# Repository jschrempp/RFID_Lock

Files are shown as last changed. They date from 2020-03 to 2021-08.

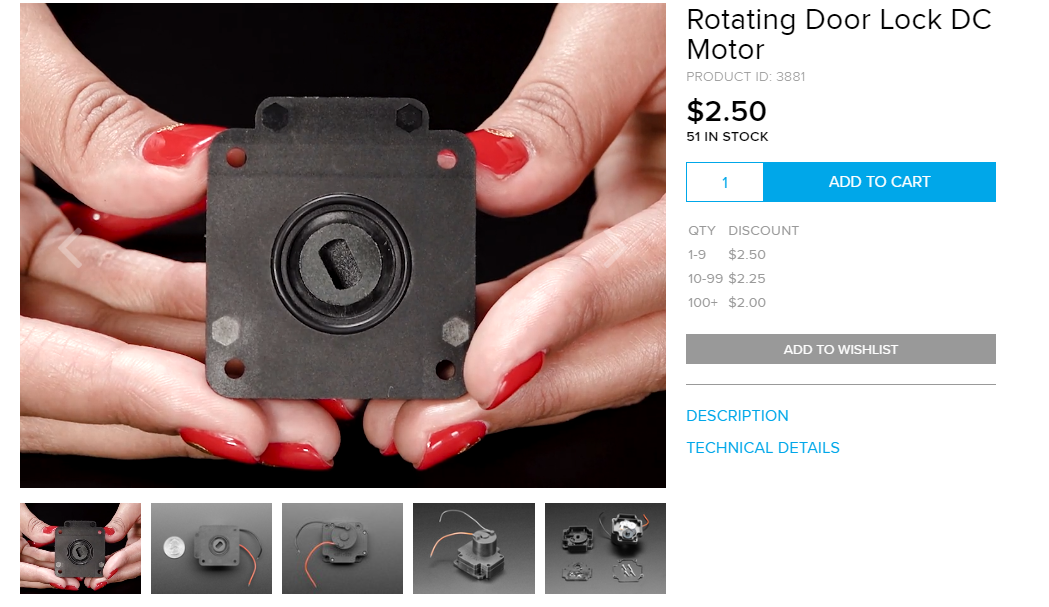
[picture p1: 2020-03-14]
Hardware/Other_Mechanisms/Adafruit_lock.png

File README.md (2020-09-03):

# RFID_Lock

Hardware and firmware for a Photon-based device that can control various locking mechanisms.

The device subscribes to publications with the name "checkin". These events are published by an RFID Station. 
The event data is JSON encoded and includes the deviceType of the publisher, as well as a secret security key.

Each lock station is configured via an App (or via the Particle Cloud) to act on a checkin event from a particular deviceType. 
If the event contains the correct deviceType and the correct secret key, then this device will unlock a cabinet, door, machine or power.

## Story
Our MN_ACL project (https://github.com/TeamPracticalProjects/MN_ACL) creates an infrastructure for secure, 
RFID-based access control to a Makerspace and it's various internal equipment locations.  That project integrates
Particle Argon-based RFID stations with a commercial cloud CRM system and an internal tracking database.
The MN_ACL project ensures that people who access the facility are paid up members in good standing and that
members who access certain locations containing sophisticated industrial equipment have basic operating 
and safety instruction credentials.  The project controls access via red/green lit buttons and an audible beeper.

Certain locations within the Makerspace contain expensive materials, parts and accessories.  We decided to create 
a Particle Photon-based add-on that could subscribe to publications sent by the Argons in the RFID stations
and unlock cabinets containing these expensive accessories.  We therefore needed to find an inexpensive but 
effective electrically controlled locking mechanism and create a Photon-based printed circuit board (and
associated Particle firmware) to unlock the cabinet when a member taps into one of the relevant RFID
stations with credentials that allow them access to these accessories.

COVID-19 related health and safety regulations require that the front door be locked to the outside and 
access to the facility be controlled. There is a 24 volt (DC) solenoid in the door mechanism that is wired 
back into the facility equipment room.  We determined that mounting an RFID station at the front entrance and 
using the same publish/subscribe mechanism as for cabinet locks, we could remotely and securely activate the front 
door solenoid lock to admit members when they tap their badge to the front door RFID station.

We decided to generalize this mechanism as much as possible in order to accommodate other access control requirements as
they arise in the future.

We decided that we needed a separate WiFi enabled circuit board for this purpose because:

1. The relationship between RFID stations and cabinets/locks is many to many.

2. Hardwiring a lock control signal from an RFID station to certain cabinets or locks is both inconvenient
and easily hacked.

3. A general-purpose, secure, WiFi enabled locking mechanism is a worthwhile and useful project
in and of itself, independent of the MN_ACL project and it's RFID stations.

We selected the Particle Photon for this project because it provides a low cost and secure means of WiFi
control and communication and because of Particle's simple and elegant cloud communication capabilities.

## Locking Mechanisms
### Locking a cabinet
We investigated a number of solutions for electrically controlled locking mechanisms and we ultimately
decided to hack an off-the-shelf mechanism from Tokatuker; see: 
https://www.amazon.com/Tokatuker-Electronic-Cabinet-Hidden-Drawer/dp/B075QF1VPR

The Tokatuker cabinet lock is a complete RFID solution in itself, but it does not have the required 
security or database integrations required for this project.  We therefore removed the electronics 
and provided our own Photon-based hardware to control the lock.  We also removed the batteries and 
we power the Tokatuker mechanism from our hardware so that the cabinets would not be stuck locked 
if a battery runs down.

We chose the Tokatuker solution because the locking mechanism itself is very innovative and uses only
a small, low power DC motor to control a mechanically robust locking system.  We found that pulsing this
motor for 30 milliseconds in one direction unlocks the lock and pulsing it for 30 milliseconds in the 
opposite direction re-locks the lock.  Unlocking the lock springs the cabinet door open and the door can
thereafter be closed and will lock anytime after the small motor returns to the locked position. The 
device can therefore unlock, opening the cabinet door, and then immediately re-lock and the door can 
be closed and will automatically lock at any time thereafter.

### The front door
The facility front door has a locking pushbar that includes a solenoid for remote unlocking.  This solenoid
was already wired back to the facility's equipment room. We experimentally determined that activating the 
solenoid for 2 seconds after a successful RFID card tap-in by a member in good standing is more than sufficient 
to provide entry to the facility.

### Our documentation
This project contains complete instructions for building an RFID Lock using the Tokatuker product.  This
project also contains instructions and firmware for activating a door-unlocking solenoid.
We also investigated various other locking mechanisms based upon servos, solenoids, etc.
We have included some information about these other approaches in this repository but we cannot
supply complete mechanics and Particle firmware to use them, as we did not carry these other locking
solutions through to a complete project solution.

## Electronics
We developed a printed circuit board that houses a Photon and integrates the Photon with components
that allowed us to test out various locking solutions.  This printed circuit board seemed so generally
useful to us that we have made it a project unto itself.  See: 
https://github.com/TeamPracticalProjects/Wireless_IO_Board

This project uses the Wireless_IO_Board hardware and we have added the Particle firmware necessary
to subscribe to publications from MN_ACL RFID Stations.  The documentation included with this project
provides ample references to these other projects where necessary.  Two sets of firmware are documented:
(1) firmware to respond to valid check-in events and unlock the modified Tokatuker motor lock.
(2) firmware to respond to valid check-in event and activate a door unlock solenoid.

## Mechanics
The modifications to the Tokatuker lock are documented in this repository.  Likewise, instructions
are provided for mounting the hardware in a small test cabinet that is demonstrative but also
useful in its own right.

## Firmware
This project includes Particle firmware (source code) for the Photon that integrates the RFID Lock
into the complete MN_ACL access control solution.

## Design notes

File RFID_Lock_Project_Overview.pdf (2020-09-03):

P a g e | 1

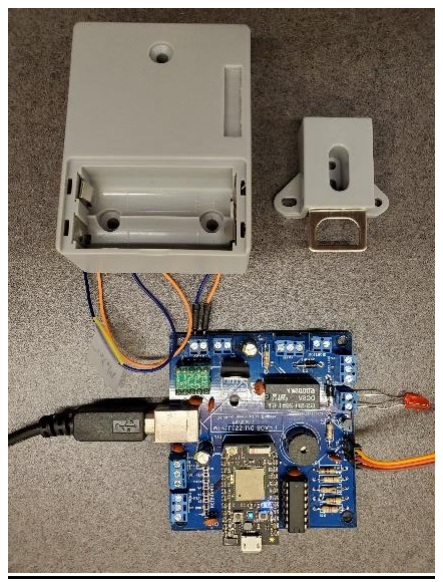
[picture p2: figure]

© 2020, Team Practical Projects, Jim Schrempp and Bob Glicksman; all rights reserved. Subject to “Terms of Use, License and Disclosure”

# RFID Lock Project Overview

By: Bob Glicksman, Jim Schrempp; v3, 8/30/20

© 2020 Team Practical Projects, Bob Glicksman and Jim Schrempp. All rights reserved.

NOTICE: Use of this document is subject to the terms of use described in the document “Terms_of_Use_License_and_Disclaimer” that is included in this release package. This document can be found at:

https://github.com/TeamPracticalProjects/Wireless_IO_Board/blob/master/Terms_of_Use_License_and_Disclaimer. pdf

© 2020, Team Practical Projects, Jim Schrempp and Bob Glicksman; all rights reserved.

## Contents

© 2020, Team Practical Projects, Jim Schrempp and Bob Glicksman; all rights reserved.

1.INTRODUCTION.

This document provides a brief overview of the RFID Lock project. Section 2 of this document describes the project in the context of the Maker Nexus RFID Access Control system project, and the Wireless I/O Board project, both of which are published at:

https://GitHub.com/TeamPracticalProjects

Section 3 of this document describes the layout of this repository and what information is included here.

2.RFID Lock Project Overview.

2.1. What this project is about.

This project is fundamentally about the hardware and firmware for a Particle¹ Photon-based device that can control various locking mechanisms. One specific locking mechanism has been fully implemented (see: https://www.amazon.com/Tokatuker-Electronic-Cabinet-Hidden-Drawer/dp/B075QF1VPR) (https://www.amazon.com/Tokatuker-Electronic-Cabinet-Hidden-Drawer/dp/B075QF1VPR) and is fully documented here. We have also implemented a solenoid lock activation mechanism to unlock a door. Other possible locking mechanisms have been briefly explored and some information about them has been included in the repository, albeit these other mechanisms have not been fully implemented and tested.

This project was specifically undertaken as an enhancement to the Maker Nexus RFID Access Control System (see: https://github.com/TeamPracticalProjects/MN_ACL). The concept is to have the MN_ACL RFID Stations publish a “check-in event” to the Particle cloud whenever a user taps into that Station with valid credentials. Every RFID Lock board subscribes to this event and compares the Station’s deviceType (included in the event) to its internally configured “Lock Listen code”. If the published deviceType matches the Lock Listen code, and if a secret key in the “check-in event” is valid, the device opens the lock. Depending upon the mechanical aspects of the lock in question, a cabinet or door may “pop open” when this happens, or else it may unlatch for some pre-specified period of time. A modified Tokatuker locking mechanism that has been fully implemented is of the type that pops a cabinet door or draw open. A solenoid controlled door unlocking mechanism has also been fully implemented and unlocks the door for a pre-specified period of time.

RFID Lock configuration can be performed via the MN_Station_Configurator App that is part of the MN_ACL project or via the Particle Console. Figure 1 below depicts the interactions of an

1 Particle.io

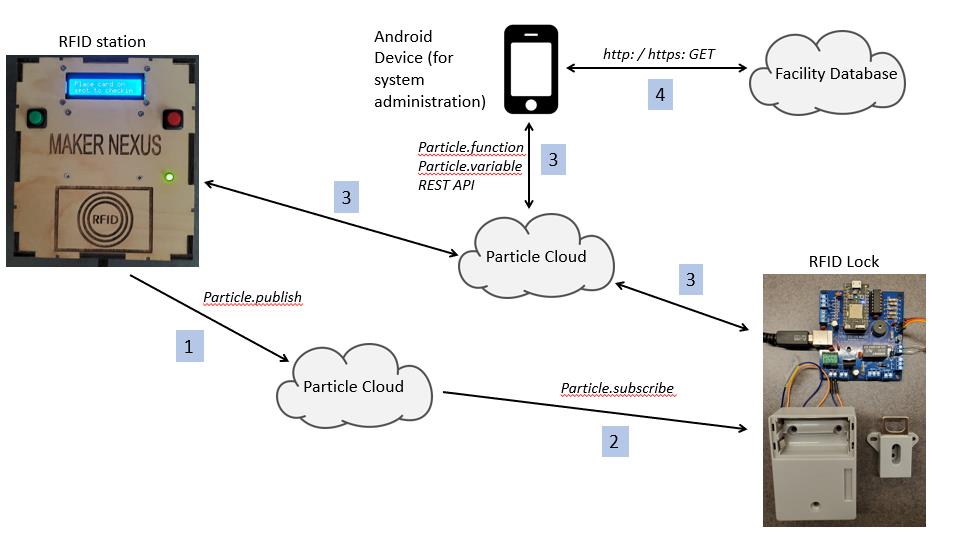
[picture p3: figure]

© 2020, Team Practical Projects, Jim Schrempp and Bob Glicksman; all rights reserved.

RFID Station, RFID Lock and MN_Station_Configurator App, all via the Particle Cloud. Further information about system operation can be found in the document:

https://github.com/TeamPracticalProjects/MN_ACL/blob/master/Documents/RFID_ACS_Overview_Document.pdf (https://github.com/TeamPracticalProjects/MN_ACL/blob/master/Documents/RFID_ACS_Overview_Document.pdf)

Figure 1. RFID Lock Architecture in Context of MN_ACS.

Referring to figure 1, the dataflows are:

(1). RFID Stations publish check-in events to the Particle cloud whenever a user taps in with a valid RFID card and the user is authorized to that Station’s function. The check-in event contains the RFID Station’s type and a facility secret key in a JSON encoded data set.

(2). RFID Locks subscribe to check-in events via the Particle cloud. When a check-in event’s deviceType data matches the Lock Listen code configured for the RFID Lock, and the check-in event’s secret key is valid, the RFID Lock unlocks the electromechanical lock to which it is wired.

(3). The MN_Station_Configurator App, running on an Android phone or tablet, allows a system administrator to configure deviceTypes into the RFID Stations, and both deviceTypes and Lock Listen Codes into RFID_Locks. The App does this by calling Particle cloud functions on these devices and the App obtains station configuration information by reading Particle cloud variables from these devices. The App (source code and install file) can be found at:

https://github.com/TeamPracticalProjects/MN_ACL/tree/master/Software/Android_Apps

© 2020, Team Practical Projects, Jim Schrempp and Bob Glicksman; all rights reserved.

The RFID Lock is made from a Photon based electronic printed circuit board and associated electromechanical locking hardware. The details of the printed circuit board are available in the following repository:

https://github.com/TeamPracticalProjects/Wireless_IO_Board

Although this project was driven by specific requirements of the Maker Nexus RFID Access Control project, the hardware, software and firmware may be useful in other contexts.

2.2. Story.

The MN_ACL project (https://github.com/TeamPracticalProjects/MN_ACL) creates an infrastructure for secure, RFID-based access control to a Makerspace and it's various internal equipment locations. That project integrates Particle Argon-based RFID stations with a commercial cloud CRM system and an internal tracking database. The MN_ACL project ensures that people who access the facility are paid up members in good standing and that members who access certain locations containing sophisticated industrial equipment have basic operating and safety instruction credentials. The project controls access via red/green illuminated buttons and an audible beeper.

Certain locations within the Makerspace contain expensive materials, parts and accessories. We decided to create a Particle Photon-based add-on that could subscribe to publications sent by the Argons in the RFID stations and unlock cabinets containing these expensive accessories. We therefore needed to find an inexpensive but effective electrically controlled locking mechanism and create a Photon-based printed circuit board (and associated Particle firmware) to unlock the cabinet when a member taps into one of the relevant RFID stations with credentials that allow them access to these accessories.

COVID-19 related health and safety regulations require that the front door be locked to the outside and access to the facility be controlled. There is a 24 volt (DC) solenoid in the door mechanism that is wired back into the facility equipment room. We determined that mounting an RFID station at the front entrance and using the same publish/subscribe mechanism as for cabinet locks, we could remotely and securely activate the front door solenoid lock to admit members when they tap their badge to the front door RFID station.

We decided to generalize this mechanism as much as possible in order to accommodate other access control requirements as they arise in the future.

We decided that we needed a separate WiFi enabled circuit board for this purpose because:

- The relationship between RFID stations and cabinets/locks is many to many.

© 2020, Team Practical Projects, Jim Schrempp and Bob Glicksman; all rights reserved.

- Hardwiring a lock control signal from an RFID station to certain cabinets or locks is both inconvenient and easily hacked.
- A general-purpose, secure, WiFi enabled locking mechanism is a worthwhile and useful project in and of itself, independent of the MN_ACL project and it's RFID stations.

We selected the Particle Photon for this project because it provides a low cost and secure means of WiFi control and communication and because of Particle's simple and elegant cloud communication capabilities.

2.3. Locking Mechanisms.

We investigated a number of solutions for electrically controlled locking mechanisms and we ultimately decided to hack an off-the-shelf mechanism from Tokatuker; see:

https://www.amazon.com/Tokatuker-Electronic-Cabinet-Hidden-Drawer/dp/B075QF1VPR

The Tokatuker cabinet lock is a complete RFID solution in itself, but it does not have the required security or database integrations required for this project. We therefore removed the electronics and provided our own Photon-based hardware to control the lock. We also removed the batteries and we power the Tokatuker mechanism from our hardware so that the cabinets would not be stuck locked if a battery runs down.

We chose the Tokatuker solution because the locking mechanism itself is very innovative and uses only a small, low power DC motor to control a mechanically robust locking system. We found that pulsing this motor for 30 milliseconds in one direction unlocks the lock and pulsing it for 30 milliseconds in the opposite direction re-locks the lock. Unlocking the lock springs the cabinet door open and the door can thereafter be closed and will lock anytime after the small motor returns to the locked position. The device can therefore unlock, opening the cabinet door, and then immediately re-lock and the door can be closed and will automatically lock at any time thereafter.

The facility front door has a locking pushbar that includes a solenoid for remote unlocking. This solenoid was already wired back to the facility's equipment room. We experimentally determined that activating the solenoid for 2 seconds after a successful RFID card tap-in by a member in good standing is more than sufficient to provide entry to the facility.

This project contains complete instructions for building an RFID Lock using the Tokatuker product. This project also contains instructions and firmware for activating a door-unlocking solenoid. We also investigated various other locking mechanisms based upon servos, solenoids, etc. We have included some information about these other approaches in this repository but we cannot supply complete mechanics and Particle firmware to use them, as we did not carry these other locking solutions through to a complete project solution.

© 2020, Team Practical Projects, Jim Schrempp and Bob Glicksman; all rights reserved.

2.4. Electronics.

We developed a printed circuit board that houses a Photon and integrates the Photon with components that allowed us to test out various locking solutions. This printed circuit board seemed so generally useful to us that we have made it a project unto itself. See:

https://github.com/TeamPracticalProjects/Wireless_IO_Board

This project uses the Wireless_IO_Board hardware and we have added the Particle firmware necessary to subscribe to publications from MN_ACL RFID stations. The documentation included with this project provides ample references to these other projects where necessary.

2.5. Mechanics.

The modifications to the Tokatuker lock are documented in this repository. Likewise, instructions are provided for mounting the hardware in a small test cabinet that is demonstrative but also useful in its own right.

2.6. Firmware.

This project includes Particle firmware (source code) for the Photon that integrates the RFID Lock into the complete MN_ACL access control solution. Two sets of firmware are documented:

- firmware to respond to valid check-in events and unlock the modified Tokatuker motor lock.
- firmware to respond to valid check-in event and activate a door unlock solenoid.

3.Repository Contents.

3.1. Repository (Top Level).

The top level of this repository contains the following documents:

- “Terms_Of_Use_License_And_Disclaimer.pdf”: this document contains the license and copyright information about the information in this repository and limitations on its

© 2020, Team Practical Projects, Jim Schrempp and Bob Glicksman; all rights reserved.

use. You must read and agree to all of the statements in this document before you are permitted to use any of the information in this repository for any reason whatsoever.

- “RFID_Lock_Project_Overview.pdf”: This is the document that you are reading. It contains an overview of the project and a guide to what is in this repository.
- “Readme.md”: This is a markdown document that contains the overview material found on the home page of this repository.
- “.gitattributes”: This is a GitHub-generated file with repository information. It contains information for GitHub, but nothing specific to this project. You do not need to open this file to use the material in this repository.
3.2. Documents.

This folder contains the project documentation:

- “RFID_Lock_Build_Instructions.pdf”: This document provides step-by-step instructions to build an RFID lock, including assembling the Wireless I/O Board, modifying the Tokatuker lock, installing the firmware on the Particle Photon, and assembling the hardware into a candidate cabinet.
- “Solenoid_Lock_Build_Instructions.pdf”: This document provides step-by-step instructions to build a device to activate a solenoid lock, including assembling the Wireless I/O Board, installing the firmware on the Particle Photon, and assembling the hardware into an enclosure.
- “Tokatuker_Cabinet_Digital_Lock_Testing.pdf”: This is a report of our investigations, experiments and findings about the Tokatuker lock and how it might be operated from a Particle Photon.
3.3. Hardware/Other Mechanisms.

This folder contains information about other electro-mechanical lock mechanisms that we surveyed. As of this date, we have not tested any of these other mechanisms. However, we feel that some of these other locks may be appropriate for situations where the Tokatuker lock is unsuitable; e.g. where it is undesirable to have the lock mechanism pop open the cabinet door or draw.

© 2020, Team Practical Projects, Jim Schrempp and Bob Glicksman; all rights reserved.

3.4. Software/Particle_SW/LockFirmware.

This folder, and its included subfolders, contains the firmware for the Particle Photon. Download this folder to your computer. You can then point the Particle Workbench IDE to this subfolder in order to:

- View the Particle source code.
- Compile the source code (locally or via the cloud).
- Flash the code to your Photon device.

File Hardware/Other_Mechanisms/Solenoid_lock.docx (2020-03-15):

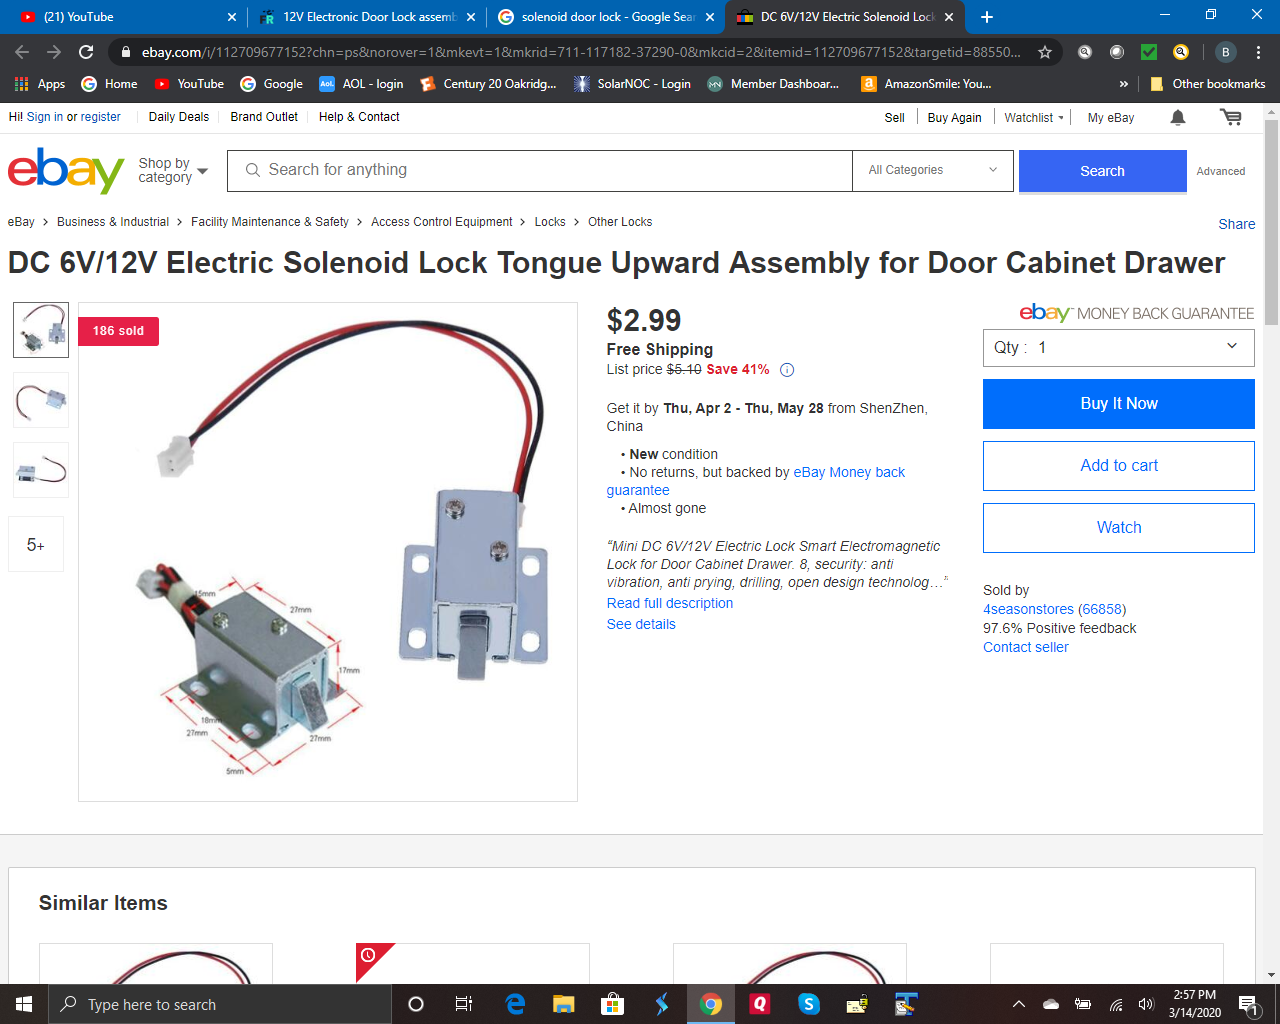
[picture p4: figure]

https://www.ebay.com/i/112709677152?itemid=112709677152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

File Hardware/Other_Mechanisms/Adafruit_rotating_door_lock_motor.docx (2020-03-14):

URL:

https://www.adafruit.com/product/3881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


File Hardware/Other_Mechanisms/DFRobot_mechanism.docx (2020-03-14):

URL:

https://www.dfrobot.com/product-1856.html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

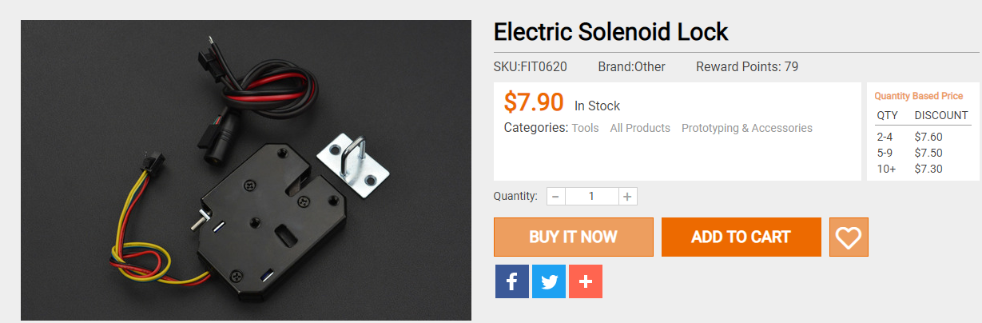
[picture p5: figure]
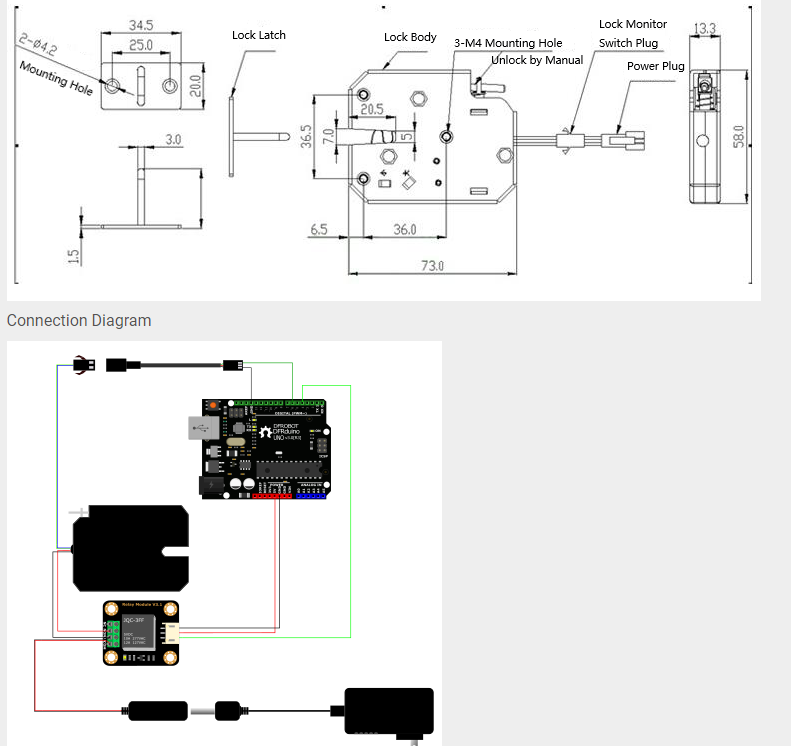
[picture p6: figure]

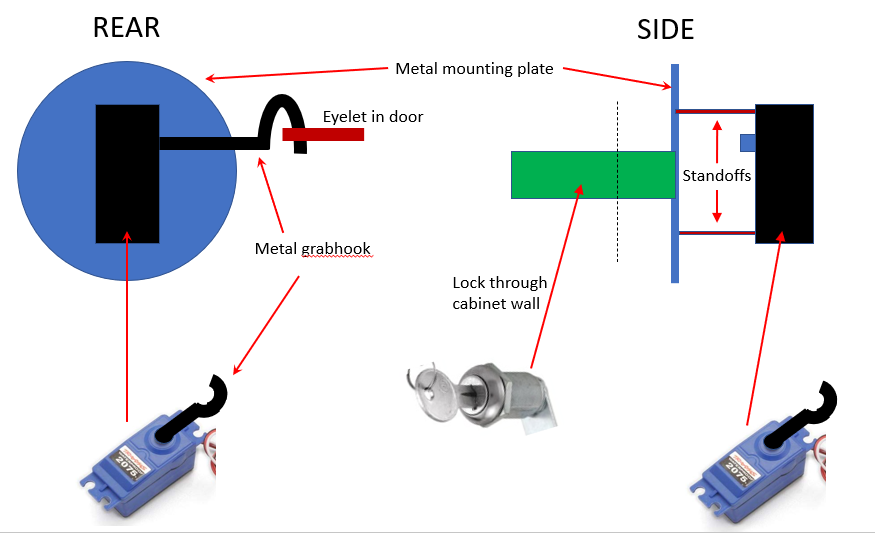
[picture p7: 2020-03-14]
Hardware/Other_Mechanisms/Concept.png

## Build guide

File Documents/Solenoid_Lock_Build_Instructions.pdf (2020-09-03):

P a g e | 1


© 2020, Team Practical Projects, Jim Schrempp and Bob Glicksman; all rights reserved. Subject to “Terms of Use, License and Disclosure”

# Solenoid Lock Build Instructions

By: Bob Glicksman, Jim Schrempp; 8/31/20

© 2020 Team Practical Projects, Bob Glicksman and Jim Schrempp. All rights reserved.

NOTICE: Use of this document is subject to the terms of use described in the document “Terms_of_Use_License_and_Disclaimer” that is included in this release package. This document can be found at:

https://github.com/TeamPracticalProjects/Wireless_IO_Board/blob/master/Terms_of_Use_License_and_Disclaimer. pdf

© 2020, Team Practical Projects, Jim Schrempp and Bob Glicksman; all rights reserved.

## Contents

© 2020, Team Practical Projects, Jim Schrempp and Bob Glicksman; all rights reserved.

1.Introduction.

This document provides step-by-step instructions to build an RFID Lock that unlocks a door or cabinet using a solenoid. This particular installation activates an existing 24 volt DC solenoid inside of a locking pushbar industrial front door. However, these instructions apply to activation of any DC solenoid up to 24 volts DC and up to 2 amperes of current.

The RFID Lock is compatible with the MN_ACS RFID Access Control System, see the following for details:

https://github.com/TeamPracticalProjects/MN_ACL

The main activity involved in this project is building a Wireless_IO_Board with the necessary components installed to operate the solenoid. The resulting Wireless_IO_Board should be mounted in a suitable enclosure and wired to a source of solenoid power and to the solenoid itself. The Wireless_IO_Board must also be supplied with its own, 5 volt logic power.

In order to integrate this locking mechanism with the MN_ACL RFID Station project, the “SolenoidFirmware” must be flashed into the Photon on the Wireless_IO_Board and the resulting Solenoid_Lock must be configured to listen for “front door” checkin events.

Each of these activities is covered in its own section of this document. Before proceeding with any of these activities, we strongly suggest that you read through the Overview document in this repository:

https://github.com/TeamPracticalProjects/RFID_Lock/blob/master/RFID_Lock_Project_Overvie w.pdf (https://github.com/TeamPracticalProjects/RFID_Lock/blob/master/RFID_Lock_Project_Overview.pdf)

2.Building the Wireless_IO_Board.

Complete instructions for building a Wireless_IO_Board can be found at:

https://github.com/TeamPracticalProjects/Wireless_IO_Board/blob/master/Docs/Wireless_IO_Board_Build_Instructions.pdf (https://github.com/TeamPracticalProjects/Wireless_IO_Board/blob/master/Docs/Wireless_IO_Board_Build_Instructions.pdf)

The minimum parts needed to operate a solenoid locking device are the Core Components (section 2.1 of the referenced document) and the Relay/Solenoid Control Parts (section 2.3 of the referenced document). You might wish to review all the Wireless_IO_Board repository; in particular the documents:

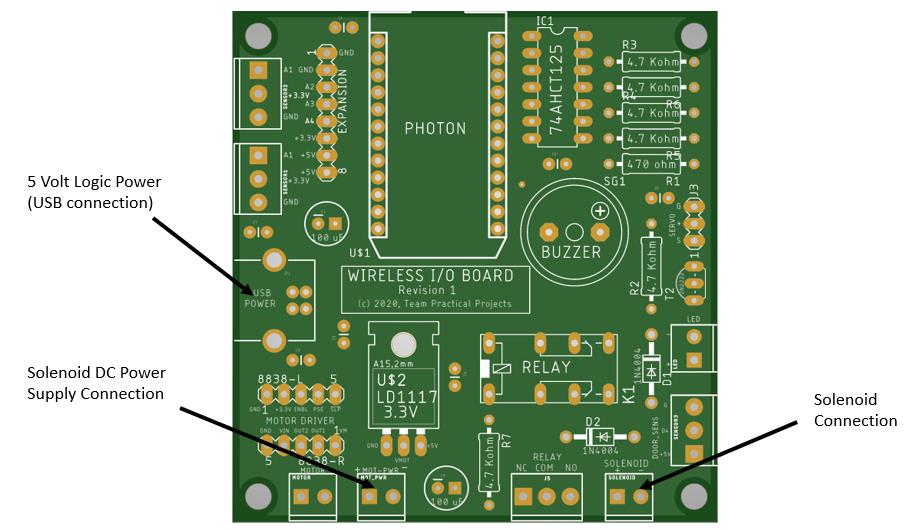
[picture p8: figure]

© 2020, Team Practical Projects, Jim Schrempp and Bob Glicksman; all rights reserved.

- https://github.com/TeamPracticalProjects/Wireless_IO_Board/blob/master/Docs/Wireless_IO_Board_User_Manual.pdf (https://github.com/TeamPracticalProjects/Wireless_IO_Board/blob/master/Docs/Wireless_IO_Board_User_Manual.pdf)
- https://github.com/TeamPracticalProjects/Wireless_IO_Board/blob/master/Hardware/PCB/Wireless_IO_Board_Parts_List.pdf (https://github.com/TeamPracticalProjects/Wireless_IO_Board/blob/master/Hardware/PCB/Wireless_IO_Board_Parts_List.pdf)

You may, of course, wish to add additional parts to your Wireless_IO_Board if your project requires additional capabilities; e.g. an external LED, an on-board buzzer, or sensor input(s).

3.Connect and Test the Solenoid Lock.

Figure 3-1 shows the external connections to the Wireless_IO_Board that you constructed per section 2 of this document.

Figure 3-1. Connections to the Wireless IO Board to Solenoid Activation.

The Solenoid Lock PCB requires two power supply connections and provides one connection to the solenoid device:

- Logic Power: 5 volt logic power is connected to the type B USB port on the Wireless_IO_Board. This connection supplies power for the circuitry on the board.

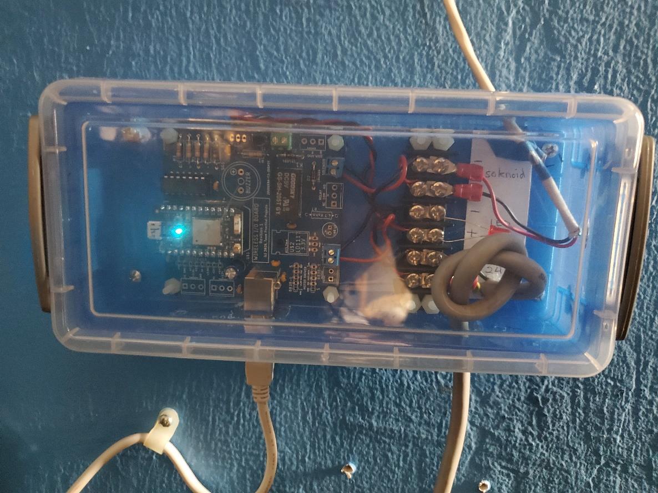
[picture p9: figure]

© 2020, Team Practical Projects, Jim Schrempp and Bob Glicksman; all rights reserved.

- Solenoid Power: A separate power supply is needed for the solenoid. In our case, this is a 24 volt DC power supply. The power supply outputs (+ and -) are connected to the Wireless_IO_Board via the Motor Power terminal block. NOTE: the Wireless_IO_Board must not have an LD1117 voltage regulator mounted on the board, nor should it have the R7 resistor and associated 100 uF capacitor mounted in the board (unless these components are needed for use with the particular solenoid power supply chosen). Carefully observe the polarity of the power supply connection – the polarity does matter!
- Solenoid Connection. Wires from the solenoid are connected to the Solenoid terminal block on the Wireless_IO_Board. This terminal block is labeled with the polarity of the solenoid output signal, in the event that this matters to the particular solenoid device used (it usually doesn’t). NOTE: the Wireless_IO_Board has a flyback diode wired across the solenoid terminals so that an external flyback diode is not needed.

We suggest mounting the completed Wireless_IO_Board in a plastic box and using an external terminal block to make connections to the solenoid and solenoid power supply wiring; see figure 3-2. This setup provides for covering of the electronics and for additional strain relief of the cables from the solenoid and solenoid power supply.

Figure 3-2. Solenoid Lock PCB and Terminal Block in Enclosure.

© 2020, Team Practical Projects, Jim Schrempp and Bob Glicksman; all rights reserved.

You can optionally test out the functionality of the solenoid lock by using the Wireless_IO_Board test firmware. This firmware is described in section 3 of the Wireless_IO_Board User Manual, which can be found at:

https://github.com/TeamPracticalProjects/Wireless_IO_Board/blob/master/Docs/Wireless_IO_Board_User_Manual.pdf (https://github.com/TeamPracticalProjects/Wireless_IO_Board/blob/master/Docs/Wireless_IO_Board_User_Manual.pdf)

4.Install and Configure the Solenoid Lock Firmware.

The firmware flashed to the Photon on the Wireless_IO_Board per section 3 of this document is used for testing purposes. In order to have your Solenoid_Lock become part of the Maker Nexus Access Control System (MN_ACS) and respond to RFID card taps on RFID Stations, you must flash different firmware onto the Wireless_IO_Board Photon. The firmware that you need is located in this repository at:

https://github.com/TeamPracticalProjects/RFID_Lock/tree/master/Software/Particle_SW

Download the folder “SolenoidFirmware” to your computer. Next, open the Particle Workbench¹ on your computer and set the “workspace” to this folder. You can compile and flash the firmware to your Photon device using the Particle Workbench. Using the Particle Workbench is beyond the scope of this document. Refer to Particle’s on-line documentation and tutorials for details.

Once the Solenoid_Lock firmware is flashed to your Wireless_IO_Board Photon, you should see the D7 LED flashing blue about once per second. You must now use the “MN_Station_Configurator” App (running on an Android device) to set the “deviceType” and the “Lock Listen code” into the Wireless_IO_Board Photon. Complete instructions for this can be found at:

https://github.com/TeamPracticalProjects/MN_ACL/blob/master/Documents/RFID_Administrator_User_Manual.pdf (https://github.com/TeamPracticalProjects/MN_ACL/blob/master/Documents/RFID_Administrator_User_Manual.pdf)

1
If you don’t have the Particle Workbench (Visual Studio Code) on your computer, see Particle’s documentation at: https://www.particle.io/workbench. Refer the Particle’s documentation for installation and operating instructions.

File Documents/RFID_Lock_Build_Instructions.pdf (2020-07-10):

P a g e | 1


© 2020, Team Practical Projects, Jim Schrempp and Bob Glicksman; all rights reserved. Subject to “Terms of Use, License and Disclosure”

# RFID Lock Build Instructions

By: Bob Glicksman, Jim Schrempp; 7/10/20

© 2020 Team Practical Projects, Bob Glicksman and Jim Schrempp. All rights reserved.

NOTICE: Use of this document is subject to the terms of use described in the document “Terms_of_Use_License_and_Disclaimer” that is included in this release package. This document can be found at:

https://github.com/TeamPracticalProjects/Wireless_IO_Board/blob/master/Terms_of_Use_License_and_Disclaimer. pdf

© 2020, Team Practical Projects, Jim Schrempp and Bob Glicksman; all rights reserved.

## Contents

© 2020, Team Practical Projects, Jim Schrempp and Bob Glicksman; all rights reserved.

1.Introduction.

This document provides step-by-step instructions to build an RFID Lock based upon the Tokatuker cabinet locking device, see:

https://www.amazon.com/Tokatuker-Electronic-Cabinet-Hidden-Drawer/dp/B075QF1VPR

The RFID Lock is compatible with the MN_ACS RFID Access Control System, see the following for details:

https://github.com/TeamPracticalProjects/MN_ACL

There are three main activities involved in this process:

- Build a Wireless_IO_Board with the necessary components installed to operate the Tokatuker device.
- Modify the Tokatuker device for use with the Wireless_IO_Board.
- Connect the modified Tokatuker device to the Wireless_IO_Board and test it out.

There are two additional (optional) activities that may be performed after these three essential steps are complete:

- Install the RFID_Lock firmware in the Wireless_IO_Board Photon and configure the RFID_Lock to listen for RFID Station check-in events.
- Mount the Tokatuker lock device and locking hasp into a cabinet.

Each of these activities is covered in its own section of this document. Before proceeding with any of these activities, we strongly suggest that you read through the Overview document in this repository:

https://github.com/TeamPracticalProjects/RFID_Lock/blob/master/RFID_Lock_Project_Overvie w.pdf (https://github.com/TeamPracticalProjects/RFID_Lock/blob/master/RFID_Lock_Project_Overview.pdf)

2.Building the Wireless_IO_Board.

Complete instructions for building a Wireless_IO_Board can be found at:

https://github.com/TeamPracticalProjects/Wireless_IO_Board/blob/master/Docs/Wireless_IO_Board_Build_Instructions.pdf (https://github.com/TeamPracticalProjects/Wireless_IO_Board/blob/master/Docs/Wireless_IO_Board_Build_Instructions.pdf)

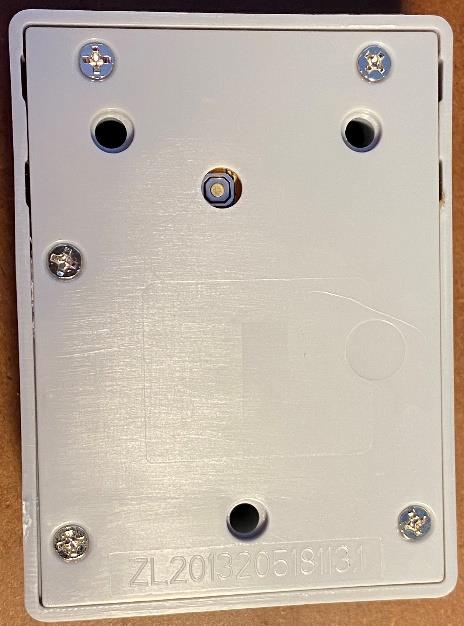
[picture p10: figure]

© 2020, Team Practical Projects, Jim Schrempp and Bob Glicksman; all rights reserved.

The minimum parts needed to operate the Tokatuker locking device are the Core Components (section 2.1 of the referenced document) and the Small Motor Controller Parts (section 2.2 of the referenced document). You might wish to review all the Wireless_IO_Board repository; in particular the documents:

- https://github.com/TeamPracticalProjects/Wireless_IO_Board/blob/master/Docs/Wireless_IO_Board_User_Manual.pdf (https://github.com/TeamPracticalProjects/Wireless_IO_Board/blob/master/Docs/Wireless_IO_Board_User_Manual.pdf)
- https://github.com/TeamPracticalProjects/Wireless_IO_Board/blob/master/Hardware/PCB/Wireless_IO_Board_Parts_List.pdf (https://github.com/TeamPracticalProjects/Wireless_IO_Board/blob/master/Hardware/PCB/Wireless_IO_Board_Parts_List.pdf)

You may, of course, wish to add additional parts to your Wireless_IO_Board if your project requires additional capabilities; e.g. an external LED, an on-board buzzer, or sensor input(s).

3.Modify the Tokatuker Device.

The following steps are required to modify the Tokatuker locking device for use on this project. In essence, these modifications involve removing the antenna and electronics board from the device and notching the case to bring out the electronic board connector which contains the locking motor wires.

Figure 3-1 shows the rear of the Tokatuker locking device. Five Phillips head screws hold the cover to the device.

Figure 3-1. Tokatuker Lock Rear View.

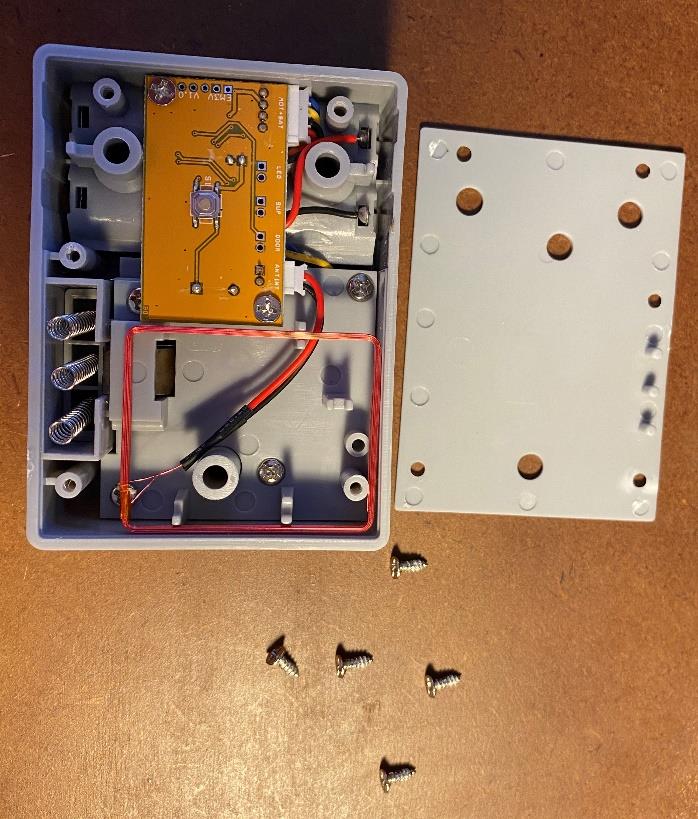
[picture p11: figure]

© 2020, Team Practical Projects, Jim Schrempp and Bob Glicksman; all rights reserved.

Remove the five screws holding the back cover to the device, revealing the internals; see figure 3-2. Note the three springs shown in the lower left side of figure 3-2. Leave these springs intact – don’t lose them! Note that when reassembling the back cover to the unit, these three springs will seat into the three bumps on the inside of the back cover. Note also the RFID loop antenna in the lower part of figure 3-2 and the electronics board in the upper part of figure 3-2. The electronics board is held in place with two more Phillips head screws.

Figure 3-2. Tokatuker Lock Back Cover Removed.

Carefully remove the two Phillips head screws that hold the electronics board in place. Next, carefully lift the RFID loop antenna and electronics board out of the unit – see figure 3-3.

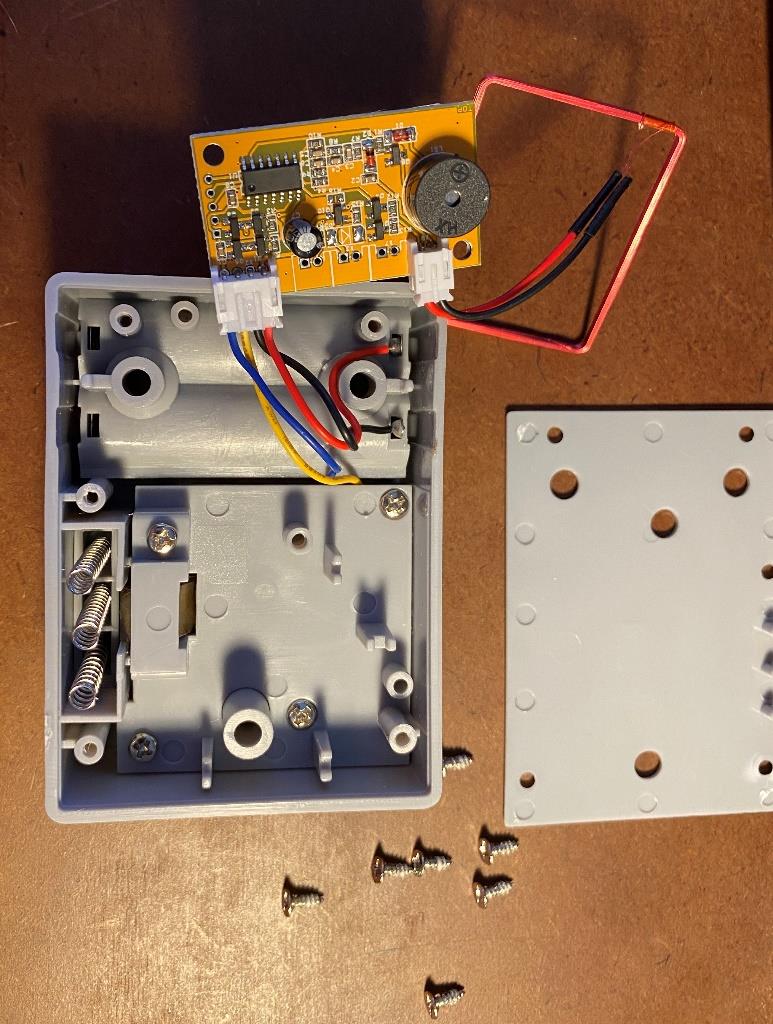
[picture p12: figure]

© 2020, Team Practical Projects, Jim Schrempp and Bob Glicksman; all rights reserved.

Figure 3-3. Antenna and Circuit Board Removed.

The electronics board has two connectors: a 2-pin connector for connecting the RFID Antenna to the electronics board and a 4-pin connector from the electronics board into the interior of the unit. Unplug the male cable 4-pin connector from the female socket on the electronics board. You can now discard the RFID loop antenna and electronics board; they are not needed for the RFID Lock project. See figure 3-4, below.

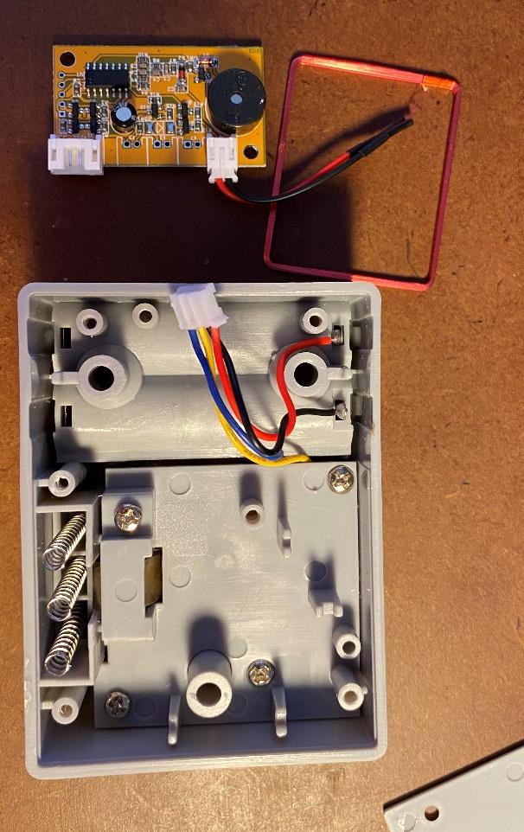
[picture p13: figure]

© 2020, Team Practical Projects, Jim Schrempp and Bob Glicksman; all rights reserved.

Figure 3-4. Antenna and Circuit Board Unplugged.

The 4-pin male connector needs to become accessible from outside of the re-assembled unit. Take a small file and cut a notch in the top side or the long side of the unit so that the cable can protrude through the side of the unit after the back cover is replaced. See figure 3-5 for an example.

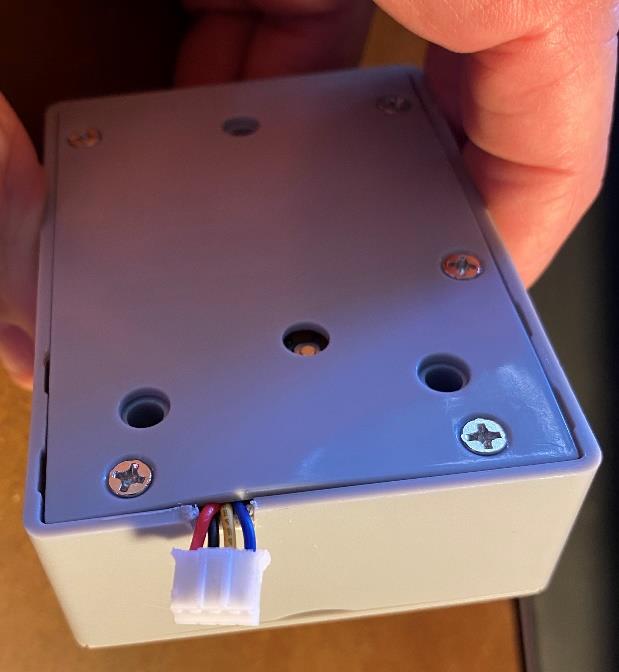
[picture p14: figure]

© 2020, Team Practical Projects, Jim Schrempp and Bob Glicksman; all rights reserved.

Figure 3-5. Back Cover Replaced with Connector Through Notch.

Place the cable through the notch that you cut and now replace the back cover on the unit, making sure that the three bumps on the inside of the back cover each engage one of the three springs that were noted in figure 3-2. Make sure that each spring is properly engaged in its bump. Now use the five original Phillips head screws to re-fasten the back cover to the unit. The reassembled unit should look similar to figure 3-5.

4.Connect and Test the RFID Lock.

The lock unit connects to the Wireless_IO_Board using two of the four wires on the connector that is exposed through the side of the unit. The wires on this connector are as follows:

- BLUE: lock unit motor +
- YELLOW: lock unit motor –
- BLACK: lock unit battery –
- RED” lock unit battery +

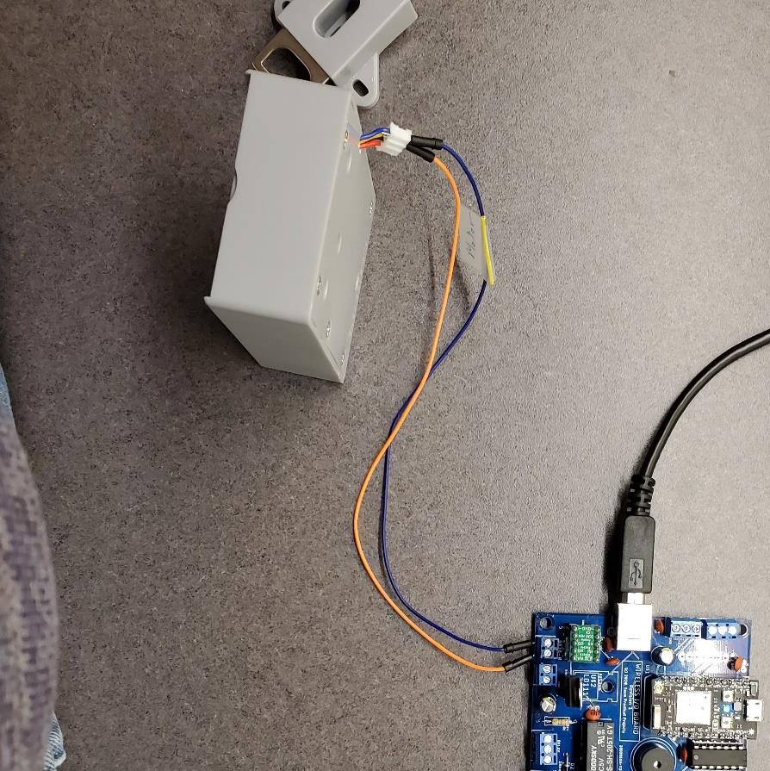
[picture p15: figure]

© 2020, Team Practical Projects, Jim Schrempp and Bob Glicksman; all rights reserved.

You will not place batteries in the unit. The Wireless_IO_Board supplies its own motor power. Therefore, the red and black leads will not be used. Wire the blue and yellow leads to the Wireless_IO_Board motor terminal block, as follows:

- BLUE wire to the outside connector of the motor terminal block
- YELLOW wire to the inside connector of the motor terminal block

See figure 4-1. For details. We have found that male-male jumpers (such as those used for solderless breadboards) work fine for this purpose, but you can use any wires that work.

Figure 4-1. Wiring the modified lock unit to the Wireless_IO_Board.

You can use the program “locktest.ino” to test out the modified lock unit connection to the Wireless_IO_Board. Complete instructions can be found in section 3 of the document:

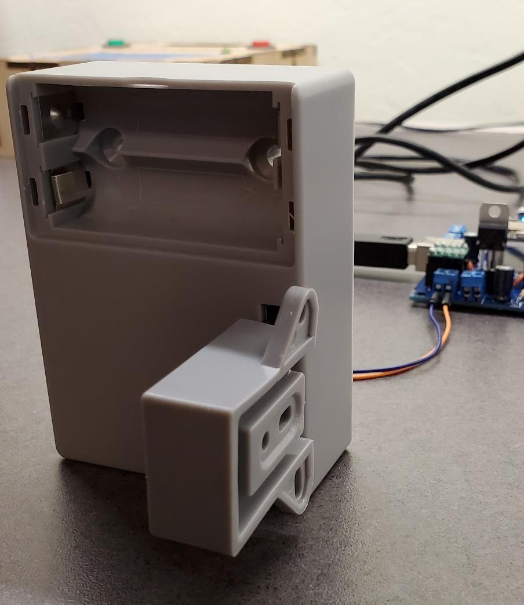
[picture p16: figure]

© 2020, Team Practical Projects, Jim Schrempp and Bob Glicksman; all rights reserved.

https://github.com/TeamPracticalProjects/Wireless_IO_Board/blob/master/Docs/Wireless_IO_Board_User_Manual.pdf (https://github.com/TeamPracticalProjects/Wireless_IO_Board/blob/master/Docs/Wireless_IO_Board_User_Manual.pdf)

You can trip the lock by using the Particle console to call the function “tripLock”. No arguments are necessary. The other functions available on the console are not applicable to these instructions and won’t perform any useful actions.

In order to test that the lock is properly wired to the Wireless_IO_Board, insert the locking hasp into the lock unit, as shown in figure 4-2. Note the proper orientation of the hasp!

*** WARNING *** Make sure that you keep your face, hands and other parts of your body away from the front of the lock unit when a hasp is inserted. When the lock is tripped, the hasp is ejected with considerable force! Keep all objects (particularly yourself) at least 6 feet away from the front of the lock unit!

Figure 4-2. Hasp inserted in the Lock.

© 2020, Team Practical Projects, Jim Schrempp and Bob Glicksman; all rights reserved.

With the hasp inserted into the lock unit as shown in figure 4-2, and keeping well clear of the front of the lock unit, click “CALL” by the “tripLock” function on the Particle console to call this function. The lock unit should click, ejecting the hasp, and then (after 2 seconds), the lock unit should click again. After this second click, the lock unit is reset and the hasp will lock into the lock unit again.

NOTE: If you hear the unit click but the hasp is not ejected, or if the hasp won’t lock into the lock unit to begin with, then you probably have the lock motor leads connected backwards! Carefully check the connections – the polarity matters!

5.Install and Configure the RFID Lock Firmware.

The firmware flashed to the Photon on the Wireless_IO_Board per section 4 of this document is used for testing purposes. In order to have your RFID_Lock become part of the Maker Nexus Access Control System (MN_ACS) and respond to RFID card taps on RFID Stations, you must flash different firmware onto the Wireless_IO_Board Photon. The firmware that you need is located in this repository at:

https://github.com/TeamPracticalProjects/RFID_Lock/tree/master/Software/Particle_SW

Download the folder “LockFirmware” to your computer. Next, open the Particle Workbench¹ on your computer and set the “workspace” to this folder. You can compile and flash the firmware to your Photon device using the Particle Workbench. Using the Particle Workbench is beyond the scope of this document. Refer to Particle’s on-line documentation and tutorials for details.

Once the RFID_Lock firmware is flashed to your Wireless_IO_Board Photon, you should see the D7 LED flashing blue about once per second. You must now use the “MN_Station_Configurator” App (running on an Android device) to set the “deviceType” and the “Lock Listen code” into the Wireless_IO_Board Photon. Complete instructions for this can be found at:

https://github.com/TeamPracticalProjects/MN_ACL/blob/master/Documents/RFID_Administrator_User_Manual.pdf (https://github.com/TeamPracticalProjects/MN_ACL/blob/master/Documents/RFID_Administrator_User_Manual.pdf)

1
If you don’t have the Particle Workbench (Visual Studio Code) on your computer, see Particle’s documentation at: https://www.particle.io/workbench. Refer the Particle’s documentation for installation and operating instructions.

© 2020, Team Practical Projects, Jim Schrempp and Bob Glicksman; all rights reserved.

6.Mount the RFID Lock in a Cabinet.

The RFID Lock can mount in most any cabinet or drawer. We have found a handy little inexpensive cabinet that is suitable for holding keys and other small parts that might need to be secured from casual use by unauthorized personnel. See:

https://www.amazon.com/Darice-Unfinished-Wooden-Hinged-Multicolor/dp/B00KNAPNWW

This section contains some suggestions about mounting the RFID Lock into this cabinet.

NOTE: We have chosen to mount the lock device and hasp with screws that go through the cabinet cover and side wall. This means that someone could gain access to the inside of the cabinet by unscrewing these screws. If this is not OK with you, we suggest that you use blind headed screws, pop rivets, super glue or some other means of mounting the lock device and hasp that cannot be removed from the outside of the cabinet. You will also have to find a way to secure the cover hinges from removal, as they come mounted with two Phillips head screws each. However, if you make these changes to our design, please make note that there may be no way to open the cabinet if the lock device mechanism fails!

Step #1 is to remove the hinged hasp and locking ring from this cabinet. Each part is secured to the cabinet by two small Phillips head screws. Leave the front cover hinges in place.

Next, remove the wires between the Wireless_IO_Board and the lock device. Insert the locking hasp into the lock device in the correct locking position, see figure 6-1.

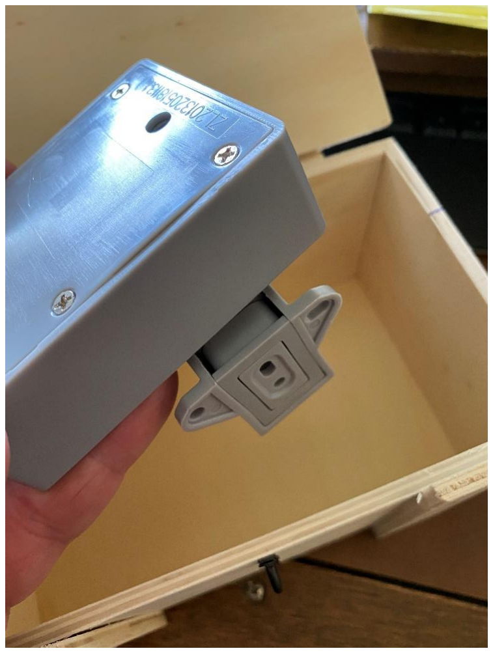
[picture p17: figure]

© 2020, Team Practical Projects, Jim Schrempp and Bob Glicksman; all rights reserved.

Figure 6-1. Positioning Lock and Hasp for Mounting.

Determine where in the cabinet you wish to mount the locking device. The locking device mounts to the inside swing cover of the cabinet. The hasp mounts on the inside side of the cabinet. The Wireless_IO_Board mounts on the back wall of the cabinet, with a hole drilled into the side or back of the cabinet to feed the USB power cable to the Wireless_IO_Board.

The lock device and hasp must align properly when they are individually mounted to the cabinet cover and side. The old adage of “measure twice and cut once” applies here! Carefully place the assembly of lock and hasp in the box and carefully align them so that the back of the lock device is flush with the inside surface of the cover when it is closed and the hasp is flush with the inside side wall of the cabinet. Carefully mark these positions on the cabinet, see figures 6-1 and 6-2.

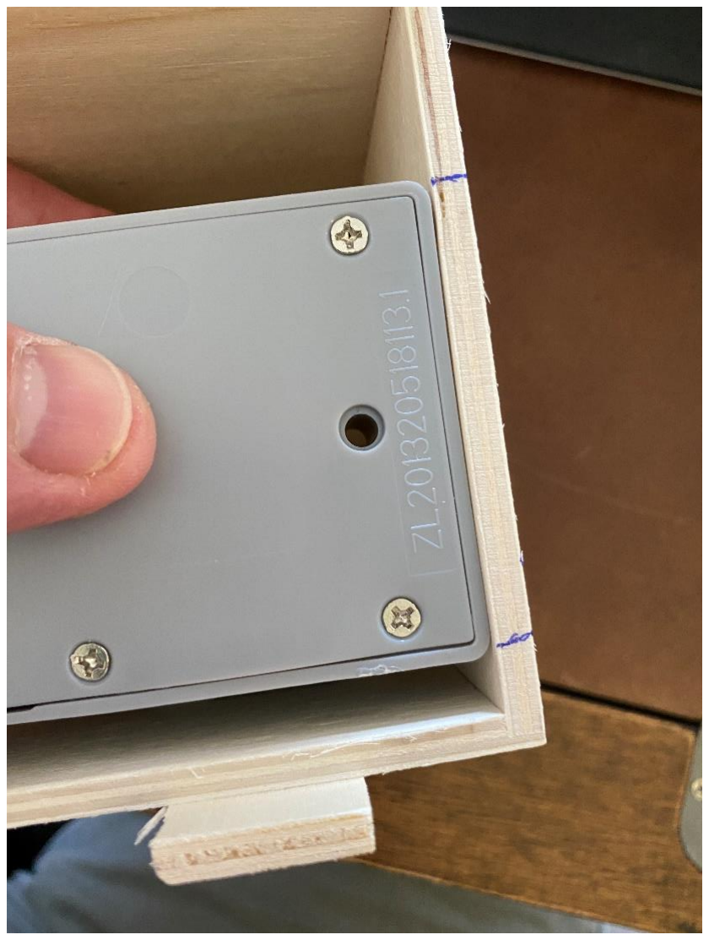
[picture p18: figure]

© 2020, Team Practical Projects, Jim Schrempp and Bob Glicksman; all rights reserved.

Figure 6-2. Mark Mounting Locations for Lock and Hasp

The locking device will mount to the inside of the cabinet cover with three screws (in the holes provided through the device). The hasp will mount to the inside of the side wall of the cabinet. It is difficult to drill screw holes from the inside; therefore, we recommend that you make paper templates for drilling the holes and drill them from the outside of the cabinet. Figure 6-3 shows how we made a paper drilling template for the hasp, marking the hasp mounting holes with the lock and hasp assembled. Figure 6-4 shows how we made a paper drilling template for lock device itself.

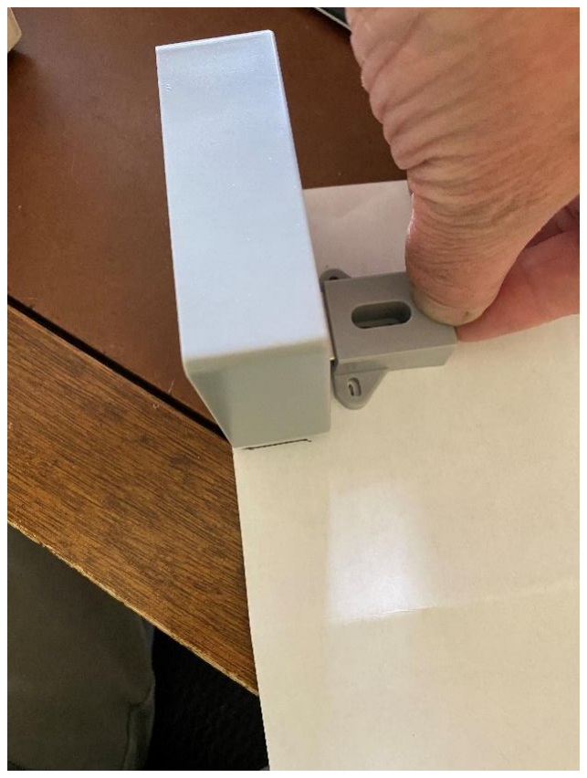
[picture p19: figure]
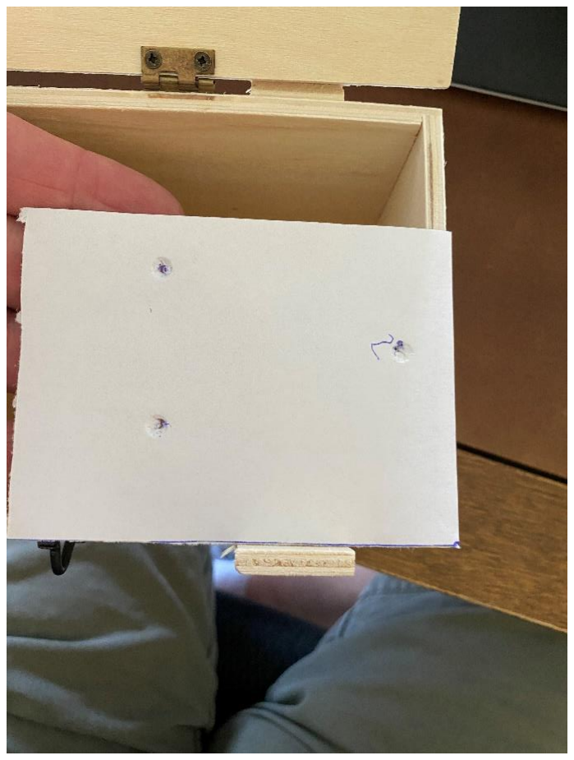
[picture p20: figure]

© 2020, Team Practical Projects, Jim Schrempp and Bob Glicksman; all rights reserved.

Figure 6-3. Mark Mounting Holes for Hasp Template.

Figure 6-4. Mark Holes for Lock Template.

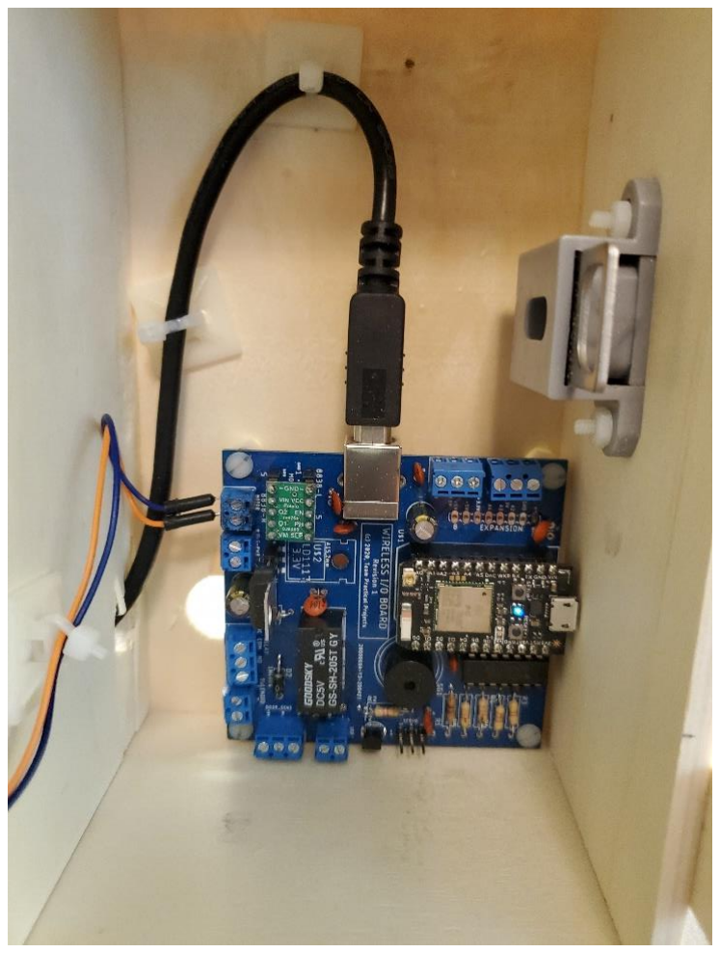
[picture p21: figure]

© 2020, Team Practical Projects, Jim Schrempp and Bob Glicksman; all rights reserved.

Carefully cut out each template and very carefully align the hasp template with the marked hasp location on the cabinet and the lock template with the marked lock device location on the cabinet cover. The templates should be taped or glued to the outside of the cabinet with the proper orientation for drilling the mounting holes. Drill mounting holes sized for the type and size of the fasteners that you have selected.

The Wireless_IO_Board has four mounting holes, one in each corner of the board. They are sized to comfortably house #6 hardware. You may use metal or nylon screws to mount the Board to the back of the cabinet; however, we suggest that you use only nylon standoffs, washers and nuts to avoid shorting out the electronic circuitry. We recommend using ½” threaded female-female nylon standoffs between the Board and the back of the cabinet. Therefore, the Board can be mounted using #6 x ¼” screws on both the cabinet side and the Board side. Once again, we suggest using nylon screws on the board side; metal screws can be used on the cabinet side if you wish. See figure 6-5, below.

Figure 6-5. Mounting and Cabling the Wireless I/O Board.

After mounting the lock device and hasp to the cabinet, DO NOT CLOSE THE CABINET DOOR or else you will lock the cabinet closed accidentally! Wire the lock device to the Wireless_IO_Board, power up the Board and check that the lock trips correctly. Only after checking this should you close the cover of the cabinet. The cabinet can now be opened by

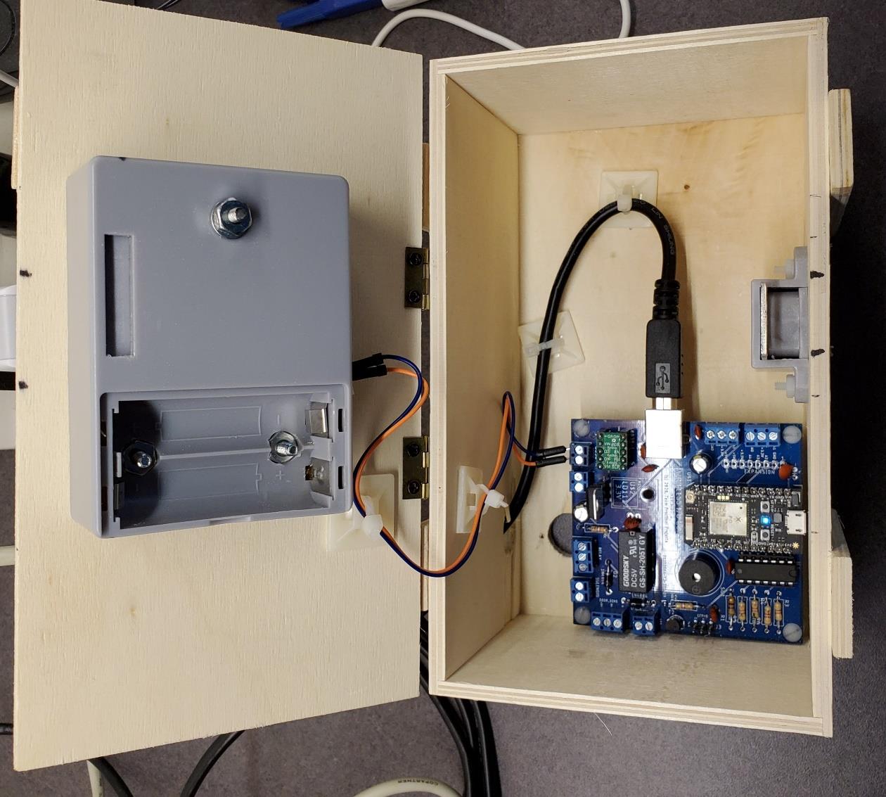
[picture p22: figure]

© 2020, Team Practical Projects, Jim Schrempp and Bob Glicksman; all rights reserved.

tripping the RFID Lock, either using the test firmware of section 4 of this document, or the RFID_Lock firmware with an RFID Station of section 5 of this document.

Dress the motor control and USB power wires using cable ties, similar to figure 6-5. Make sure that the cabinet closes and opens smoothly. The final assembly should look similar to figure 6-6.

Figure 6-6. Completed Assembly.

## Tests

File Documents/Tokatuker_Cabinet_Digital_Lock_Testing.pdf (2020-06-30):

P a g e | 1


© 2020, Team Practical Projects, Jim Schrempp and Bob Glicksman; all rights reserved. Subject to “Terms of Use, License and Disclosure”

# Tokatuker Cabinet Digital Lock Testing

By: Bob Glicksman, Jim Schrempp; 3/28/20; updated 6/29/20

© 2020 Team Practical Projects, Bob Glicksman and Jim Schrempp. All rights reserved.

NOTICE: Use of this document is subject to the terms of use described in the document “Terms_of_Use_License_and_Disclaimer” that is included in this release package. This document can be found at:

https://github.com/TeamPracticalProjects/Wireless_IO_Board/blob/master/Terms_of_Use_License_and_Disclaimer. pdf

© 2020, Team Practical Projects, Jim Schrempp and Bob Glicksman; all rights reserved.

## Contents

© 2020, Team Practical Projects, Jim Schrempp and Bob Glicksman; all rights reserved.

BACKGROUND.

The Maker Nexus RFID Access Control System development team was asked to evaluate electronic cabinet locks that could be used in conjunction with the RFID Access Control System. The basic idea is to secure (lock) a cabinet or tool-chest with one of these locks such that the locked device would be unlocked when the MN RFID Access Control System gives the “green light” for access to a particular area or item of equipment. In this manner, tooling and/or physical lock keys could be secured so that only people who are permitted to that location or equipment item can use it.

Jim Schrempp found a candidate device on the Internet:

https://www.amazon.com/Tokatuker-Electronic-Cabinet-Hidden-Drawer/dp/B075QF1VPR

Jim and Bob dissected the device and found a circuit board that provides the RFID token capability and that unlocks the lock. We unplugged the circuit board, exposing a connector with 4 wires: 2 wires supply battery (3 volt) power to the circuit board and the other two wires activate the lock mechanism. We found that by supplying battery power to the lock mechanism wires manually, we could lock and unlock the device.

We subsequently dissected the lock mechanism itself and found that the device was activated by a small 3 volt DC motor. A half turn of the motor releases the mechanism so that a locking ring can be inserted and removed. A spring loaded pusher forces the locking ring out of the mechanism when it is unlocked, thus forcing open the cabinet door or drawer. A reverse half turn of the motor locks the mechanism, allowing the locking ring to be inserted but not removed.

We then developed and tested a Particle Photon based breadboard that allows us to remotely lock and unlock the mechanism. We empirically determined the minimum time to pulse the motor to produce the half turn and which direction locks and which unlocks the mechanism. Unfortunately, we damaged the mechanism in disassembly and reassembly and the test unit does not operate reliably. Jim procured a second, factory fresh unit, and this report documents the results of tests and observations of the factory fresh unit.

OUT OF THE BOX TESTS.

The purpose of these tests is to establish a baseline operation of the unit as it is designed to work with its own, internal, electronics. I unpacked the unit, inserted batteries, programmed the master key card, and then tested the lock mechanism using the master key card. Here are my observations:

© 2020, Team Practical Projects, Jim Schrempp and Bob Glicksman; all rights reserved.

1. When the card is tapped, the device unlocks and stays unlocked for about 10 seconds, It then locks again. I don’t know why the unit stays unlocked this long, since the locking ring must be inserted when the device is in the locked state (else it will just be ejected).
2. I inserted the locking ring and then activated the device a number of times. The ring was ejected each and every time that I activated the device. I tried wiggling the ring around each time I inserted it. In the damaged unit, I was able to wiggle the ring to different positions and cause it to bind up sometimes and not be ejected when the lock is tripped. However, when I wiggled the inserted ring in the new unit, it tended to reposition itself and it ejected every single time that I operated it.
3. The unit beeps repeatedly during the 10 seconds between unlocking and locking. I assume that this is to let you know that you can’t close the cabinet or draw during this time (you can close it but it won’t lock).

BREADBOARD CONTROL TESTS.

I removed the batteries and the back cover of the new unit, revealing the circuit board and antenna:

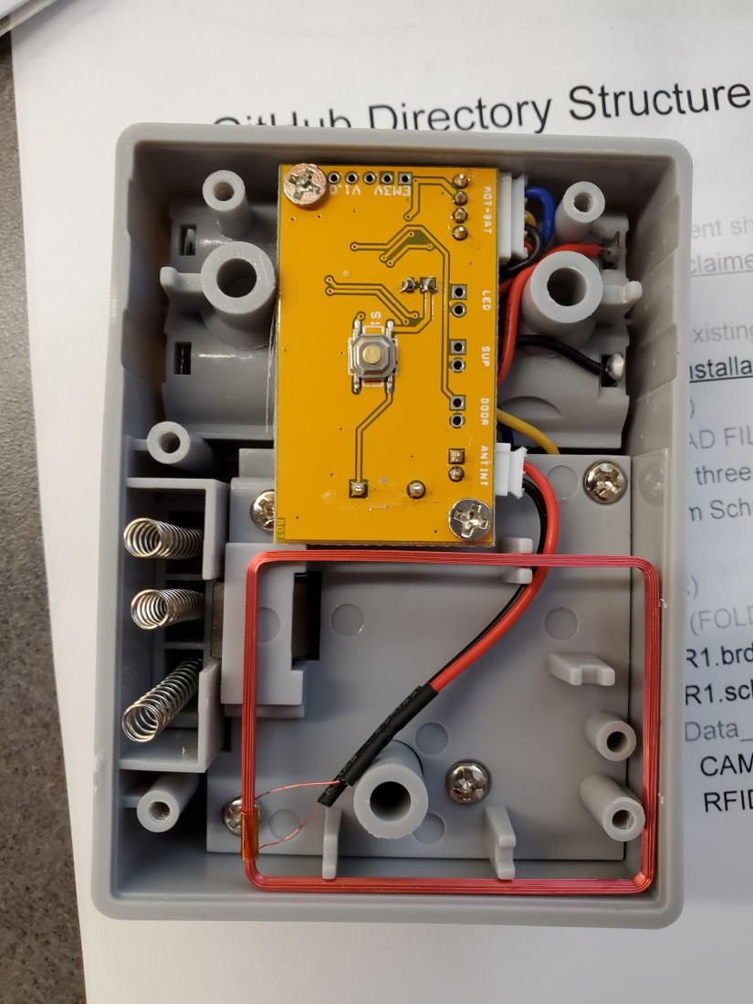
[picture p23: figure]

© 2020, Team Practical Projects, Jim Schrempp and Bob Glicksman; all rights reserved.

Next, I unplugged the RFID antenna from the circuit board and removed it:

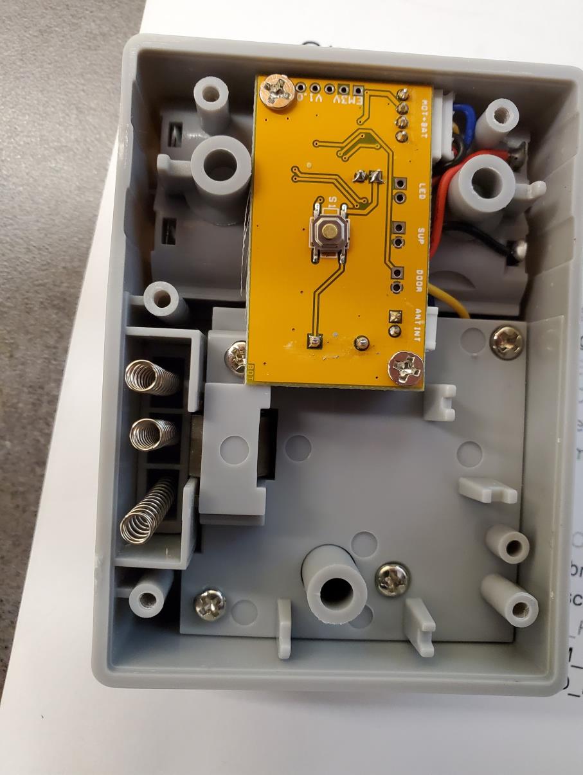
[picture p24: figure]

© 2020, Team Practical Projects, Jim Schrempp and Bob Glicksman; all rights reserved.

Next, I removed the circuit board and disconnected the remaining connector to it. This connector contains 4 wires - 2 for battery power to the circuit board and 2 for the motor:

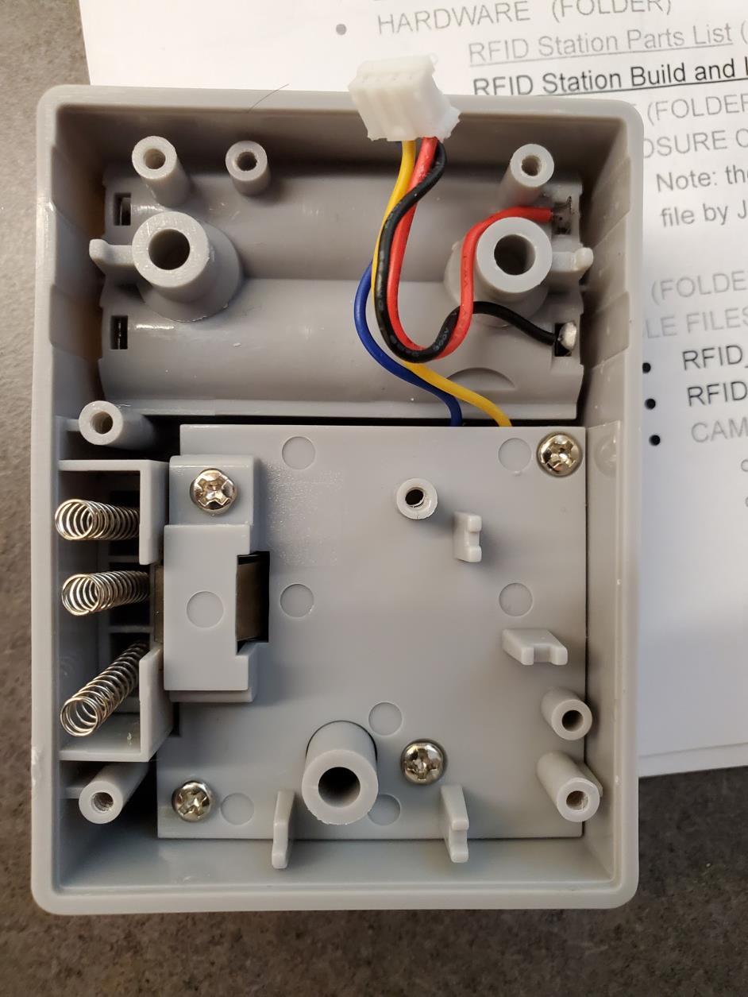
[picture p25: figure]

© 2020, Team Practical Projects, Jim Schrempp and Bob Glicksman; all rights reserved.

●

Note the 3 springs in the lower right hand side of the above photo. The back cover has three plastic protrusions that must mate with these three springs and the back cover must be replaced in order to compress these springs. These are the springs that eject the locking ring when the unit is unlocked. These springs, and the plastic piece below them, hold the mechanism open when the motor position is reversed to the lock position so that the locking ring can then be re-inserted and locked.

In order to replace the back cover while exposing the cable with the motor wires on it, I filed a notch into the back cover, as shown in the photo:

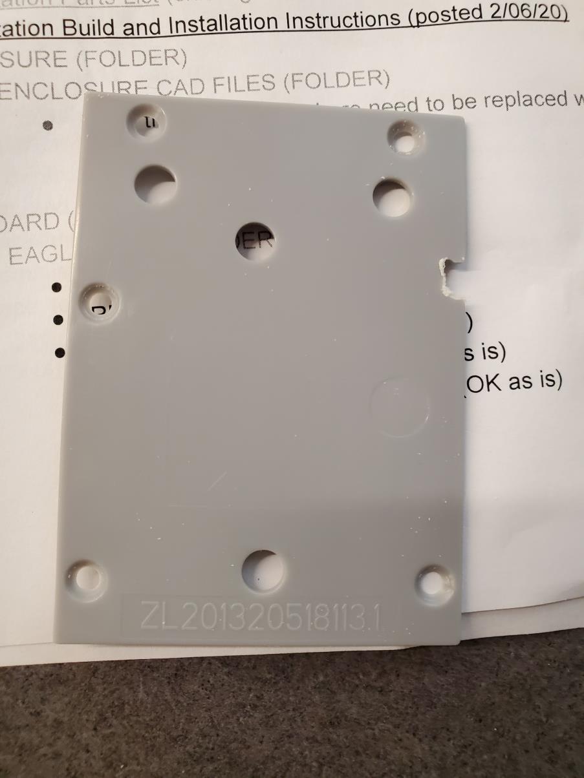
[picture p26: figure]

© 2020, Team Practical Projects, Jim Schrempp and Bob Glicksman; all rights reserved.

I then replaced the back cover, carefully running the cable wires out through the notch, and carefully aligning the protrusions on the back cover with the three springs:

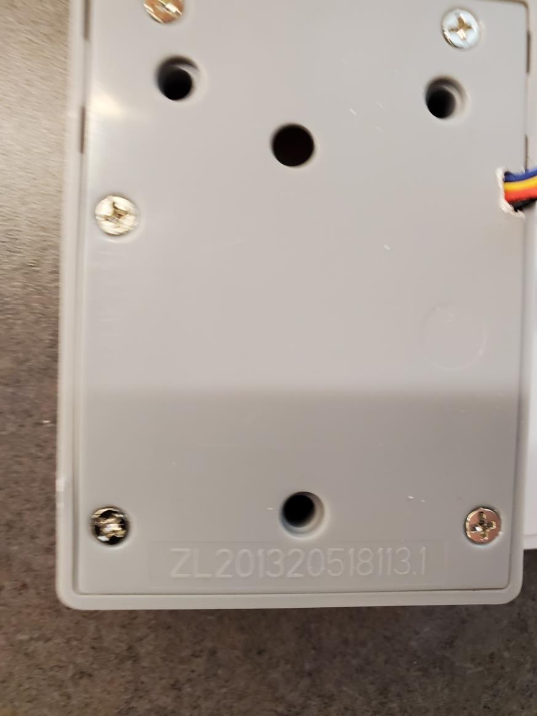
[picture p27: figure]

© 2020, Team Practical Projects, Jim Schrempp and Bob Glicksman; all rights reserved.

Finally, I connected the motor driver on the breadboard to the blue and yellow wires on the cable connector. The other two wires are left unconnected.

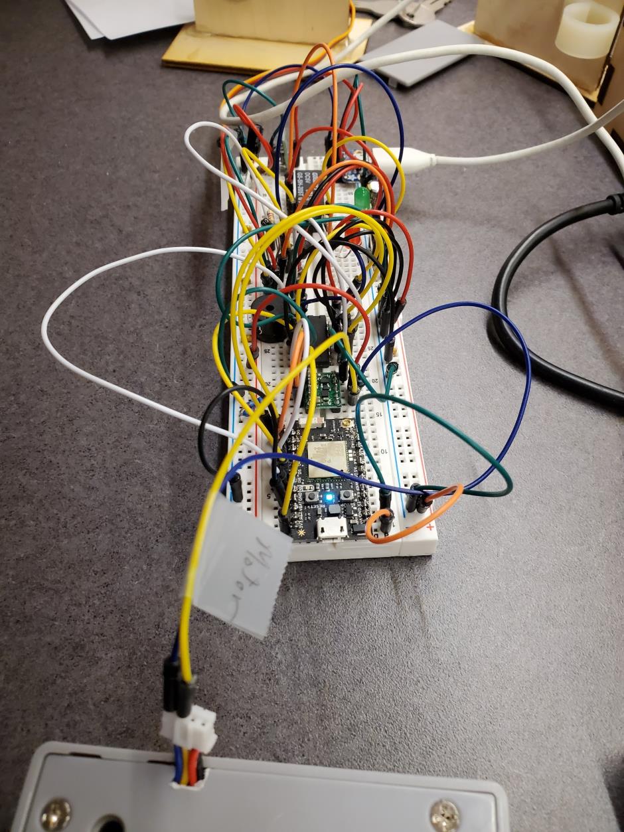
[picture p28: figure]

© 2020, Team Practical Projects, Jim Schrempp and Bob Glicksman; all rights reserved.

I can now lock and unlock the device by using the Particle console to trip the mechanism.
When the Particle cloud function tripLock() is called (with any data as the argument, even a null string), the unit unlocks for a preset time and then locks. The function that operates this unit is:

const int pulseTime = 30; // motor activation time (ms)
const int unlockTime = 2000; // unlock time for door to swing open

int tripLock(String command) { // cloud function to trip the lock unlock();
delay(unlockTime);
lock();

© 2020, Team Practical Projects, Jim Schrempp and Bob Glicksman; all rights reserved.

} // end of tripLock()

void unlock() { // unlock the latch
digitalWrite(directionPin, HIGH); // motor direction is unlock digitalWrite(runPin, HIGH);
delay(pulseTime);
digitalWrite(runPin, LOW);
} // end of unlock()

void lock() { // lock the latch
digitalWrite(directionPin, LOW); // motor direction is lock digitalWrite(runPin, HIGH);
delay(pulseTime);
digitalWrite(runPin, LOW);
} // end of lock()

The complete test code (locktest.ino) can be found at:

https://github.com/TeamPracticalProjects/Wireless_IO_Board/tree/master/Test_Firmware

Note that the 30 ms time to pulse the motor to run a half turn was empirically determined. As a follow-on exercise, I pulsed the motor for 20 ms and found that it did not travel a complete 180 degrees. Pulsing the motor for 25 ms barely made the motor turn 180 degrees; in fact, it seemed a bit short. Therefore, it seems that 30 ms is the correct motor pulse timing.

The 2 second (2000 ms) time between unlock() and lock() was arbitrary on my part. The factory unit’s operation leaves 10 seconds between unlock and lock, but I don’t know why it has to be so long.

# LOCK MECHANISM STUDY AND PULSE TIME

TESTING.

I opened the covering of the mechanical parts of the old unit and took a photo of the mechanism:

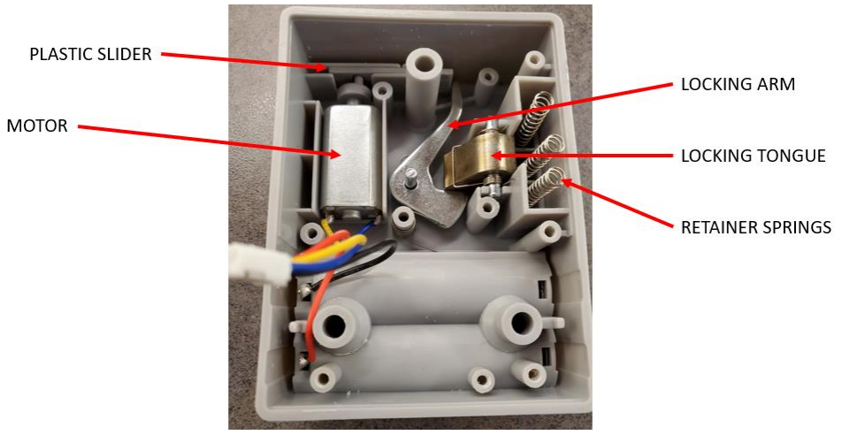
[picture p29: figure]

© 2020, Team Practical Projects, Jim Schrempp and Bob Glicksman; all rights reserved.

There is a small 3 volt DC motor in the upper left side of the unit. The motor has a cam that linearly moves a plastic slider piece, shown above the motor. The plastic slider pushes the shiny metal locking arm in the center of the photo. When the slider is pushed to the right via the motor, it allows the brass locking tongue to spring back into the locking arm’s cavity. When the motor pushes the slider back to the left (½ turn counter-clockwise), a spring on the locking arm wants to rotate the locking arm counter-clockwise so that it prevents the locking tongue from being pushed back, thus locking the mechanism.

The three springs shown in the upper right of the photo push a plastic retainer (under the springs) down toward the front of the unit. When the motor/slider is moved to the lock position, the locking arm wants to rotate counter-clockwise, but it can’t because the retainer prevents the locking tongue from springing to the right. However, when the locking ring is inserted into the slot in the front of the unit, it pushes this retainer to the back (compressing the three springs). Since the locking ring is hollow in the center, the locking tongue is now free to spring to the right and the locking arm can then rotate counter-clockwise and thus prevent the tongue from being pushed back to unlock the ring.

When the motor is activated to make a ½ turn clockwise, it pushes the plastic slider to the right which then pushes the locking arm to rotate clockwise. The spring loaded retainer has, all the while, been trying to force the locking ring out of the unit, but it couldn’t because the locking tongue could not move back to the left. But now that the motor has moved the plastic slider to the right, rotating the locking arm clockwise, the ring can be ejected from the unit pushing the locking tongue back into the cavity of the locking arm.

This very clever mechanism requires only a small current to the small DC motor (in the right direction) to operate a much stronger mechanism. The stronger forces of the mechanism come

© 2020, Team Practical Projects, Jim Schrempp and Bob Glicksman; all rights reserved.

from the various springs in the unit; specifically, the three large springs behind the plastic ring retainer. Energy to compress these springs comes not from the motor or the batteries but rather, from the user closing the cabinet door, thus forcing the locking ring into the retainer and compressing the springs.

Takeaways:
1. The unit locks via turning the motor ½ turn counter-clockwise, so that the plastic slider is all of the way to the left.
2. The unit unlocks via turning the motor ½ turn clockwise, so that the plastic slider is all of the way to the right.
3. When the unit is unlocked, the locking ring is forced out of the unit via the retainer and three large springs and the door/draw is pushed open. The plastic retainer then keeps the unit open by holding the tongue back into the cavity of the locking arm.
4. The locking ring, and thus the door/draw, cannot be closed until the motor is rotated back to the lock position.
5. Once the motor is rotated back to the lock position, the locking ring may be inserted into the unit and it will lock, until the motor is again activated to unlock the unit.

Major takeaway: the motor must be pulsed in the clockwise direction long enough to make the ½ turn (180 degrees) counter-clockwise to open the unit. The motor power is only on during this pulse time. After a short period of time, the motor must be pulsed again, this time with opposite DC polarity, to move it ½ turn counter-clockwise; back to the lock position. The motor is again unpowered and the cabinet door/draw may be closed and will automatically lock.

CONTROLLER DESIGN.

We now know that the motor must be pulsed with 3 volt DC power for 30 ms -- pulsed counter-clockwise to open the lock and eject the locking ring, and then back clockwise to lock the mechanism and enable the locking ring to be inserted and stay locked into the unit. The batteries and the internal RFID circuit board and antenna are removed and discarded. One white connector in the unit’s PC board is for the antenna, which is removed. The other connector is 4 pin connector, as follows:

- Orange: battery + to the PC board
- Black: battery - to the PC Board
- Yellow: motor + from the PC board
- Blue: motor - from the PC Board.

Only the yellow and blue connections are activated with a 3 volt, 30ms pulse -- +/- for unlock and -/+ for lock.

© 2020, Team Practical Projects, Jim Schrempp and Bob Glicksman; all rights reserved.

The controller uses a Particle Photon, a 5 volt to 3.3 volt low dropout voltage regulator (LD1117-3.3), and a low voltage H-bridge motor controller (Pololu DRV8838). The schematic can be found at:

https://github.com/TeamPracticalProjects/Wireless_IO_Board/blob/master/Hardware/PCB/Wireless_IO_Board_Rev_1_PCB_sch.pdf (https://github.com/TeamPracticalProjects/Wireless_IO_Board/blob/master/Hardware/PCB/Wireless_IO_Board_Rev_1_PCB_sch.pdf)

Note: this schematic is for a general purpose I/O board that supports this project as well as other I/O types (buzzer, LED, relay, etc.)

Two I/O pins from the Photon control the motor controller: One for the direction (DIR - Photon pin D2) and one is for the motor power pulse (RUN - Photon pin D3; to pulse the motor with power for 30 ms). The motor power comes from the 3.3 volt power supply, while the motor controller logic is powered via the Photon’s 3.3 volt power output. Particle code fragment to operate the motor was presented above.

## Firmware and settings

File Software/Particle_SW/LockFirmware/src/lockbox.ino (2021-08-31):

/*********************************************************************
 * lockbox
 * 
 * This program is used to control the locking mechanism of a box.
 * The program listens for a Particle IO event named "checkin". It then
 * examines the data of the event to see if this event should be acted upon.
 * In this first implementation it expect the event data to be a JSON package.
 * This program provides a Particle Cloud function to configure the particular
 * device number it will respond to.
 * 
 * Checkin event Base format
 *      {“deviceType”:105}
 * Extended format
 *      { “deviceType”:105, 
 *        “Modifiers”: 
 *           { 
 * 	         “Mod1”:”zyx”,
 *   	     “Mod2”: “abcs, wxy, 87r”,
 *	         “Mod3”: 5678
 * 	        }
 *       }
 *      The “Modifiers” section is to be determined as specific protocol between an RFID 
 *      station type and the lockboxes that are intended to respond. Mod1, etc are just placeholders.
 * 
 * The configuration function is:
 *      setLockListenDevType(param1)
 *      where param1 is a string representation of the device type to listen for.
 * 
 * For logging purposes these devices also have an MN Device Type set through
 *      cloudSetDeviceType(String data)
 *      
 * Hints on reading this code ...
 * The action starts when we receive a "checkin" event from the Particle Cloud. That is stowed
 * and the main loop will see it and act on it.
 * 
 * PRE RELEASE DEVELOPMENT LOG
 * 
 * (c) 2020; Team Practical Projects
 * 
 * Authors: Bob Glicksman, Jim Schrempp
 * 
 *    0.1  Just starting on it
 *    0.2  It works
 *    0.3  Added cloud function to trip lock
 *    0.3  Added validate checkin event using secret value. 
 *    0.4  Added #define in mnutils.h to prevent degbugX events that cost Particle 
 *         data operations
************************************************************************/
#define MN_FIRMWARE_VERSION 0.4

// Our UTILITIES
#include "mnutils.h"
#include "lockAction.h"
#include "rfidkeys.h"

//----------- Global Variables

// holds event data for a received checkin event
// The loopLockbox() routine waits for this to be non null and then 
// handles the event. After handling event it sets this to the null
// string and its ready to go again.
String mg_checkinEventData = "";

String g_recentErrors = "";
String debug2 = "";
int debug3 = 0;
int debug4 = 0;
int debug5 = 0;

// ------------------   Forward declarations, when needed
//


// -------------------- UTILITIES -----------------------

template <size_t charCount>
void strcpy_safe(char (&output)[charCount], const char* pSrc)
{
    // Copy the string — don’t copy too many bytes.
    strncpy(output, pSrc, charCount);
    // Ensure null-termination.
    output[charCount - 1] = 0;
}

char * strcat_safe( const char *str1, const char *str2 ) 
{
    char *finalString = NULL;
    size_t n = 0;

    if ( str1 ) n += strlen( str1 );
    if ( str2 ) n += strlen( str2 );

    finalString = (char*) malloc( n + 1 );
    
    if ( ( str1 || str2 ) && ( finalString != NULL ) )
    {
        *finalString = '\0';

        if ( str1 ) strcpy( finalString, str1 );
        if ( str2 ) strcat( finalString, str2 );
    }

    return finalString;
}  


// ------------- firmwareupdatehandler
// Called by Particle OS when a firmware update is about to begin
//
void firmwareupdatehandler(system_event_t event, int data) {
    switch (data) {
    case firmware_update_begin:

        break;
    case firmware_update_complete:
        
        break;
    case firmware_update_failed:
        
        break;
    }
}

/***************
 * heartbeatLEDs
 * 
 * Called from Loop() 
 * 
 * Will heartbeat the D7 LED so we can tell that our code is alive
 * 
 */
void heartbeatLEDs() {
    
    static unsigned long lastBlinkTimeD7 = 0;
    static int ledState = HIGH;
    const int blinkInterval = 500;  // in milliseconds
    
    if (millis() - lastBlinkTimeD7 > blinkInterval) {
        
        if (ledState == HIGH) {
            ledState = LOW;
        } else {
            ledState = HIGH;
        }
        
        digitalWrite(ONBOARD_LED_PIN, ledState);
        lastBlinkTimeD7 = millis();
    
    }
    
}

// ---------- Reboot Manager ----------
// rebootSet()
//   Called in the main loop with a 0 parameter
//   Checks to see if a reboot is pending and if so, is it time to do the reboot.
// 
//   Pass in a number of milliseconds to wait for a reboot and it will not 
//   reboot but instead it will set the reboot timer.
//   
void rebootSet(long millisecondsToWait) {

    static unsigned long rebootTime = 4294967290;  // makes it so we don't reboot as soon as the system starts

    if (millisecondsToWait > 0) {

        //set the reboot time
        rebootTime = millis() + millisecondsToWait;
    
    } else if (millis() > rebootTime) {

        System.reset();

    }

}

// ------------- Set Device Type ---------
// Called with a number to set device type to determine behavior
// Valid values are in eDeviceConfigType
//
int cloudSetDeviceType(String data) {

    int deviceType = data.toInt();

    debugEvent("devtypeinput: " + String(deviceType));

    if (deviceType == -1) {
        buzzerGoodBeepOnce();
        return EEPROMdata.deviceType;
    } else if ((deviceType) or (data == "0")) {
        int oldType = EEPROMdata.deviceType;
        logToDB("DeviceTypeChange", String(deviceType),0,"","");
        EEPROMdata.deviceType = deviceType;
        EEPROMWrite(); // push the new devtype into EEPROM 
        digitalWrite(REJECT_LED, HIGH);
        // reset variable so mainloop does not change LCD display 
        // (I admit this is a bit of a hack, but we are going to reboot right away anyway and
        //  until we do, we are technically the oldType. The type only changes on reboot.)
        EEPROMdata.deviceType = oldType;  
        rebootSet(1000);
        return 0;
    }

    return 1;

}

// ------------- Set Lock Listen Type ---------
// Called with a number to set the device type that a lock box will act upon
// Valid values are in eDeviceConfigType
//
int cloudSetLockListenDevType(String data) {

    int lockListenType = data.toInt();

    debugEvent("lockListenType: " + String(lockListenType));

    if (lockListenType == -1) {
        // Return current lockListenType
        return EEPROMdata.lockListenType;
    } else if ((lockListenType) or (data == "0")) {
        int oldType = EEPROMdata.lockListenType;
        logToDB("ListenTypeChange", String(lockListenType),0,"","");
        EEPROMdata.lockListenType = lockListenType;
        EEPROMWrite(); // push the new devtype into EEPROM 
        // reset variable so mainloop does not change LCD display 
        // (I admit this is a bit of a hack, but we are going to reboot right away anyway and
        //  until we do, we are technically the old lockListenType. The lockListenType only changes on reboot.)
        EEPROMdata.lockListenType = oldType;  
        rebootSet(1000);
        return 0;
    }

    return 1;

}

// ------------- Cloud Trip Lock  ---------
// Called to open the lock as if a checkin event was received
// The parameter is ignored.
//
int cloudTripLock(String data) {
    tripLock();
    return 0;
}



//--------------- particleEventcheckin --------------------
// 
// This routine  is registered with the particle cloud to receive any
// events that come from a device in this Particle account and 
// named "checkin"
//
void particleCallbackEventCheckin (const char *event, const char *data) {
    // hold off on debugEvent publishing while callback is active
    allowDebugToPublish = millis() + 20000;

    String eventName = String(event);
    
    // NOTE: NEVER call particle publish (incuding debugEvent) from any
    // routine called from here. Your Particle  processor will  panic

    if (eventName.indexOf("checkin") >= 0) {

        if (mg_checkinEventData.length() > 0) {
            //we have not processed the previous checkin event
            debugEvent("checkin buffer overrun");
        } else {
            mg_checkinEventData = String(data);
        }

    } else {
        // only here for debugging. In fact, there could be events that are not "checkin" and we should not care
        // debugEvent("unknown particle event 1: " + String(event));

    }

    allowDebugToPublish = millis() + 500;
    
        
}

void eventcheckin(String data) {

    const int capacity = JSON_OBJECT_SIZE(8) + 2*JSON_OBJECT_SIZE(8);
    StaticJsonDocument<capacity> docJSON;
   
    char temp[1000]; //This has to be long enough for an entire JSON response
    strcpy_safe(temp, data);

    // will it parse?
    DeserializationError err = deserializeJson(docJSON, temp );
    JSONParseError =  err.c_str();
   if (!err) {
        //We have valid full JSON response 
        int secret = docJSON["secret"];
        if (secret != checkinEventSecret ) {
            // secret did not validate, the event publisher is a fraud 
            debugEvent("received checkin with bad secret:" + String(secret));
        } else {
            // secret value was correct
            if (docJSON["deviceType"] == EEPROMdata.lockListenType) {

                tripLock();
                logToDB("Unlock", "Unlocking based on checkin of devType: " 
                        +  String((int) EEPROMdata.deviceType), 0, "", "");
                debugEvent("Unlocking based on checkin of devType: " 
                        +  String((int) EEPROMdata.deviceType) );

            } else {
                // Not the device type we are looking for
                debugEvent("received checkin event, not my devType");
            }
        }
   
    } else {
        debugEvent ("checkin event JSON parse error. " + String(temp));
    }

}





//--------------- particleCallbackMNLOGDB --------------------
// 
// This routine  is registered with the particle cloud to receive any
// events that begin with this device and "mnlogdb" or "fdb". This routine will accept
// the callback and then call the appropriate handler.
//
void particleCallbackMNLOGDB (const char *event, const char *data) {

   // hold off on debugEvent publishing while callback is active
    allowDebugToPublish = millis() + 20000;

    String eventName = String(event);
    String myDeviceID = System.deviceID();
    
    // NOTE: NEVER call particle publish (incuding debugEvent) from any
    // routine called from here. Your Particle  processor will  panic

    if (eventName.indexOf(myDeviceID + "fdbGetStationConfig") >= 0) {

        fdbReceiveStationConfig(event, data);

    } else {

        debugEvent("unknown particle event 2: " + String(event));

    }

    allowDebugToPublish = millis() + 500;
    
}




// ----------------- clearStationConfig
//
//
//
void clearStationConfig() {

    g_stationConfig.isValid = false;
    g_stationConfig.deviceType = 0;
    g_stationConfig.deviceName = "";
    g_stationConfig.LCDName = "";
    g_stationConfig.photoDisplay = "";
    g_stationConfig.logEvent = "";
    g_stationConfig.OKKeywords = "";

}

// --------------------- fdbGetStationConfig ------------
//
//
//
void fdbGetStationConfig() {

    clearStationConfig();
    String output = String(EEPROMdata.deviceType);
    Particle.publish("fdbGetStationConfig", output, PRIVATE);

}

// ----------------- fdbReceiveStationConfig ----------
//
//  fdbReceiveStationConfig
//
void fdbReceiveStationConfig(const char *event, const char *data) {

    const int capacity = JSON_OBJECT_SIZE(8) + 2*JSON_OBJECT_SIZE(8);
    StaticJsonDocument<capacity> docJSON;
   
    char temp[3000]; //This has to be long enough for an entire JSON response
    strcpy_safe(temp, data);

    // will it parse?
    DeserializationError err = deserializeJson(docJSON, temp );
    JSONParseError =  err.c_str();
    if (!err) {
        JsonObject root_0 = docJSON[0];
        //We have valid full JSON response 
        if (root_0["deviceType"].as<int>() == EEPROMdata.deviceType) {

            int devType = root_0["deviceType"].as<int>();
            String deviceName =  root_0["deviceName"].as<char*>();
            String LCDName = root_0["LCDName"].as<char*>();
            String logEvent = root_0["logEvent"].as<char*>();
            String photoDisplay = root_0["photoDisplay"].as<char*>();
            String OKKeywords = root_0["OKKeywords"].as<char*>();

            setStationConfig(
                devType,
                deviceName,
                LCDName,
                logEvent,
                photoDisplay,
                OKKeywords
            );

        } else {
            debugEvent("Station Config deviceType does not match. Expected: " 
                    + String((int) EEPROMdata.deviceType) 
                    + " received: " 
                    + String(root_0["deviceType"].as<int>()) );
            // the admin loop will be waiting for the isValid member to be true.
        }
   
    } else {
        debugEvent ("Staion Config JSON parse error. " + String(temp));
        // the admin loop will be waiting for the isValid member to be true.
    }

}




/*************** FUNCTIONS FOR USE IN REAL CARD READ APPLICATIONS *******************************/




// ------------ Functions for the Admin app 
//
//  These functions are called by the Admin Android app
//




// ---------------------- LOOP FOR equipment station ---------------------
// ----------------------                  ----------------------
// This function is called from main loop when configured for any device except admin or checkin 
//
void loopLockbox() {    
    //WoodshopLoopStates
    enum llbxState {
        llbxINIT,
        llbxWAITFOREVENTDATA,
        llbxERROR
    };
    
    static llbxState llbxloopState = llbxINIT;
    //static unsigned long processStartMilliseconds = 0; 
    
    switch (llbxloopState) {
    case llbxINIT:
        llbxloopState = llbxWAITFOREVENTDATA;
        break;
    
    case llbxWAITFOREVENTDATA:{

        if (mg_checkinEventData.length() > 0) {

            eventcheckin(mg_checkinEventData);
            mg_checkinEventData = ""; // we handled the event, so clear it

        }

        // just stay in this state
        break;
    }
    case llbxERROR:
        break;

    default:
        break;
    } //switch (mainloopState)
    


}




// ---------------- loopUndefinedDevice ------
// This is called over and over from the main loop when the
// device is configured as type 0, undefined. This is most 
// likely when the device is first set up or is undergoing some 
// hardware debug.
void loopUndefinedDevice() {

    digitalWrite(READY_LED,HIGH);
    digitalWrite(ADMIT_LED,HIGH);
    digitalWrite(REJECT_LED,HIGH);

}



// --------------------- SETUP -------------------
// This routine runs only once upon reset
void setup() {

    Particle.variable ("recentErrors",g_recentErrors);
    Particle.variable ("JSONParseError", JSONParseError);
      
    int success = 0; 
    if (success) {}; // xxx to remove warning, but should we check this below?

    // The following are useful for debugging
    //Particle.variable ("RFIDCardKey", g_clientInfo.RFIDCardKey);
    //Particle.variable ("g_Packages",g_packages);
    //success = Particle.function("GetCheckInToken", ezfGetCheckInTokenCloud);
    // xxx
    //Particle.variable ("debug2", debug2);
    //Particle.variable ("debug3", debug3);
    //Particle.variable ("debug4", debug4);
    
    // Used by all device types
    success = Particle.function("SetDeviceType", cloudSetDeviceType);

    // used by lockbox
    success = Particle.function("SetLockListenType",cloudSetLockListenDevType);
    success = Particle.function("TripLock",cloudTripLock);
   
     // Needed for all devices
    Particle.subscribe(System.deviceID() + "mnlogdb",particleCallbackMNLOGDB, MY_DEVICES); // older
    Particle.subscribe(System.deviceID() + "fdb",particleCallbackMNLOGDB, MY_DEVICES); // newer
    Particle.subscribe("checkin",particleCallbackEventCheckin, MY_DEVICES); 

    System.on(firmware_update, firmwareupdatehandler);

    allowDebugToPublish = millis();  // Allows our particle publish routines to run now

    // initialize the lockAction library
    initLockAction();

    // Gawd, dealing with dst!
    Time.zone(-8); //PST We are not dealing with DST in this device
    bool yesDST = false;
    if ( (Time.month() > 3) && (Time.month() < 11) ) {
        yesDST = true;
    }
    if ( (Time.month() == 3) && (Time.day() > 10 ) ) {
        yesDST = true;
    }
    if ( (Time.month() == 3) && (Time.day() == 10) && (Time.hour() > 2) ){
        yesDST = true;
    }
    if ( (Time.month() == 11) && (Time.day() < 3 ) ) {
        yesDST = true;
    }
    if ( (Time.month() == 11) && (Time.day() == 3) && (Time.hour() < 2) ){
        yesDST = true;
    }
    if (yesDST) {
        Time.beginDST();
        debugEvent("DST is set"); // xxx
    } 

    // read EEPROM data for device type 
    EEPROMRead();
  
    pinMode(ONBOARD_LED_PIN, OUTPUT);   // the D7 LED
    digitalWrite(ONBOARD_LED_PIN,LOW);
   
    logToDB("restart",String(MN_FIRMWARE_VERSION),0,"","" );
   
    // Signal ready to go
    //flash the D7 LED twice
    for (int i = 0; i < 2; i++) {
        digitalWrite(ONBOARD_LED_PIN, HIGH);
        delay(500);
        digitalWrite(ONBOARD_LED_PIN, LOW);
        delay(500);
    } 


}

// This routine gets called repeatedly, like once every 5-15 milliseconds.
// Spark firmware interleaves background CPU activity associated with WiFi + Cloud activity with your code. 
// Make sure none of your code delays or blocks for too long (like more than 5 seconds), or weird things can happen.
void loop() {

    // Main Loop State
    enum mlsState {
        mlsASKFORSTATIONCONFIG,
        mlsWAITFORSTATIONCONFIG,
        mlsDEVICELOOP, 
        mlsERROR
    };
    
    static mlsState mainloopState = mlsASKFORSTATIONCONFIG;
    static unsigned long processStart = 0;
    
    switch (mainloopState) {
    case mlsASKFORSTATIONCONFIG:
        if ((EEPROMdata.deviceType == DEVICETYPE_UNDEFINED) || (EEPROMdata.deviceType == DEVICETYPE_CHECKIN)) {
           
            // if type is undefined or checkin, then don't need config.
            if (EEPROMdata.deviceType == DEVICETYPE_UNDEFINED) {
                setStationConfig( DEVICETYPE_UNDEFINED, "Undefined","Undefined","Undefined","","");
            } else if (EEPROMdata.deviceType == DEVICETYPE_CHECKIN) {
                setStationConfig( DEVICETYPE_CHECKIN, "CheckIn", "Check In","Check In","","");
            } else {
                setStationConfig( 99999,"code error 1","code error 1","code error 1","","" );
            }

            mainloopState = mlsDEVICELOOP;

        } else {
            
            // type is other than undefined or checkin, get config.
            // Get config info from the Facility database
            processStart = millis();
            fdbGetStationConfig();
            mainloopState = mlsWAITFORSTATIONCONFIG;

        }

        break;

    case mlsWAITFORSTATIONCONFIG:
        if (millis() - processStart > 20000 ) {

            // Failed to get station config
            // xxx how to alert to this error??
            mainloopState = mlsERROR;

        } else if (g_stationConfig.isValid) {

            mainloopState = mlsDEVICELOOP;
        }
        // otherwise stay in this state 

        break;

    case mlsDEVICELOOP: {

        // Once the intial steps have occurred, the main loop will stay
        // in this state forever. It calls out to the correct device code and
        // the "loop" continues there

        // This version of software only supports the Lockbox
        
        // all other stations
        loopLockbox();
        
        break;
    }
    case mlsERROR: 
        mainloopState = mlsERROR; // No way out of this except a reboot
        break;

    default:
        // how to alert to this error
        mainloopState = mlsERROR;
        break;
    }
    
    heartbeatLEDs(); // heartbead on D7 LED 

    debugEvent("");  // need this to pump the debug event process

    // Reboot once a day.
    if ( (Time.hour() == 1) && (Time.minute() == 5)) {   
        // Since we only check the Minute, set the reboot to be at least one minute from now
        long rebootDelay = (int) random(70000,30000); // 70 seconds - 5 minutes
        rebootSet(rebootDelay); 
    }
    rebootSet(0); // check to see if a reboot should happen
}

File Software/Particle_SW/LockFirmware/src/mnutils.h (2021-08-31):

// This file holds common utilities that are used by modules in the RFID project
// of Maker Nexus
//
// (CC BY-NC-SA 3.0 US) 2019 Maker Nexus   https://creativecommons.org/licenses/by-nc-sa/3.0/us/
//
// Version 20200603   New definition of allowDebugToPublish
//

#include "application.h"

//#define TEST     // uncomment for debugging mode
//#define RFID_READER_PRESENT  // uncomment when an RFID reader is connected
//#define LCD_PRESENT  // uncomment when an LCD display is connected
//#define MN_PRODUCTION_COMPILE // uncomment to compile with production keys

//#define DEBUGX_EVENTS_ALLOWED  //These events consume Particle cloud Data Operations and should not be enabled for
                               //every production device for weeks at a time. 

#ifdef LCD_PRESENT
// This #include statement was automatically added by the Particle IDE.
#include <LiquidCrystal.h>   
extern LiquidCrystal lcd;
#endif

//Required to get ArduinoJson to compile
#define ARDUINOJSON_ENABLE_PROGMEM 0
#include <ArduinoJson.h>
//https://arduinojson.org/v6/assistant/

#ifndef MNUTILS_H
#define MNUTILS_H

#define IRQ_PIN D3
#define RST_PIN D4  // not connected
#define ONBOARD_LED_PIN D7

#define READY_LED D4   // xxx second definition of this pin...
#define ADMIT_LED A4
#define REJECT_LED A5
#define BUZZER_PIN D2
#define MN_EPROM_ID 453214  //This value is written to the EEPROM to show that the
                            //data is ours. Change this and every device will have to
                            //be configured again.
#define DEVICETYPE_UNDEFINED 0
#define DEVICETYPE_CHECKIN 1
#define DEVICETYPE_ADMIN 2
#define DEVICETYPE_LOCKBOX 500

struct struct_stationConfig {
    bool isValid = false;
    int deviceType;
    String deviceName;
    String LCDName;
    String photoDisplay;
    String logEvent;
    String OKKeywords;
} ;

typedef enum  {
    IN_PROCESS = 1,
    COMPLETE_OK = 2,
    COMPLETE_FAIL = 3,
    IDLE =4
} enumRetStatus;

typedef enum {
    acIDLE = 1,
    acGETUSERINFO = 2,
    acIDENTIFYCARD = 3,
    acBURNCARDNOW = 4,
    acRESETCARDTOFRESH = 5
} enumAdminCommand;

extern enumAdminCommand g_adminCommand;
extern String g_adminCommandData;
extern struct_stationConfig g_stationConfig;

// you can add more fields to the end of this structure, just don't change
// the order or size of any existing fields.
struct structEEPROMdata {
    int MN_Identifier = 11111111;  // set to MN_EPROM_ID when we write to EEPROM
    int deviceType = 0;  // Hold the value that drives the behavior of 
                         // this device. Set via Cloud Function. 
    int lockListenType = 0;  // Holds the device type that a lock box will use to
                             // know that it should act on a checkin event it receives.
} ;

// xxx this should be accessed via a function call in the module and removed from global scope
extern structEEPROMdata EEPROMdata; 

// xxx change RFIDCardKey to rfidcardmnuid
struct  struct_clientInfo {  // holds info on the current client
    String lastName = "";           // lastName
    String firstName = "";      // just the first lastName
    bool isValid = false;        // when true this sturcture has good data in it
    int clientID = 0;           // numeric value assigned by EZFacility. Guaranteed to be unique
    String RFIDCardKey = "";    // string stored in EZFacility "custom fields". We may want to change this name
    String memberNumber = "";   // string stored in EZFacility. May not be unique
    String contractStatus = ""; // string returned from EZF. Values we know of: Active, Frozen, Cancelled, Suspended
    int amountDue = 0;          // from EZF
} ;

extern struct_clientInfo g_clientInfo;

extern String JSONParseError;

extern unsigned long allowDebugToPublish;  // when false, debugEvent will hold off on publishing
                                   // needed when in a partcle cloud callback routine
 

void buzzerBadBeep();

void buzzerGoodBeepOnce();

void buzzerGoodBeepTwice();

void buzzerGoodBeeps3UpDownUp();

void writeToLCD(String line1, String line2);

//-------------- Particle Publish Routines --------------
// These routines are used to space out publish events to avoid being throttled.
//

int particlePublish (String eventName, String data); 

// Call with any message. It will be buffered and published to the particle could as 
// a debugEvent. View them in the Particle.io console.
// Call this from the main loop with a null message to keep the debug events going 
void debugEvent (String message);

// writes message to a webhook that will send it on to a cloud database
// These have to be throttled to less than one per second on each device
// Parameters:
//    logEvent - a short reason for logging ("checkin","reboot","error", etc)
//    logData - optional freeform text up to 250 characters
//    clientID - optional if this event was for a particular client 
void logToDB(String logEvent, String logData, int clientID, String clientFirstName, String clientLastName);

// similar to logToDB, but calls the webhook RFIDLogCheckInOut
void logCheckInOut(String logEvent, String logData, int clientID, String clientFirstName, String clientLastName);

// This is the return called by Particle cloud when the RFIDLogging webhook completes
//
void RFIDLoggingReturn (const char *event, const char *data);

// Write to the EEPROM 
//
// 
void EEPROMWrite ();

// Read from EEPROM
//
//
void EEPROMRead();

void clearClientInfo();

void setStationConfig(int deviceType, String deviceName, String LCDName, String logEvent, String photoDisplay, String OKKeywords);


#endif

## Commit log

2020-03-14 Populate Repository
    Initial population of reposiitory with information from tested breadboard
    [RFID_Lock_PCB.brd, RFID_Lock_PCB.sch]
2020-03-15 Consolidated firmware
    Consolidated firmware for servo, motor and I/O locks into one test routine. Deleted the previous standalone servo_lock routine. The new consolidated routine has the correct pin definitions per the Eagle schematic.
2020-03-15 Updated schematic
    Updated board schematic to wire one relay pole to support a solenoid. The second relay pole is left for general purpose use.
    [RFID_Lock_PCB.brd, RFID_Lock_PCB.sch]
2020-03-15 Placed parts on PCB
    [RFID_Lock_PCB.brd]
2020-03-16 Corrected PCB
    Corrected pin header spacing for motor driver.
    [RFID_Lock_PCB.brd, RFID_Lock_PCB.sch]
2020-03-16 Update RFID_Lock_PCB.brd
    Added mounting holes to PCB
    [RFID_Lock_PCB.brd]
2020-03-16 Update RFID_Lock_PCB.brd
    Autorouted and copper poured the .brd file. Passes DRC.
    [RFID_Lock_PCB.brd]
2020-03-18 Update locktest.ino
    Added 20 ms delay between lock() and unlock() to allow for the motor to settle down.
2020-03-18 Finalized Board File
    Added necessary silkscreen and created gerber files.
    [RFID_Lock_PCB.brd]
2020-03-28 Update locktest.ino
    Removed the extra lock() commanda to the motor lock to test with the new factory fresh locking mechanism.
2020-04-09 Create PCB_Issues_For_Rework.txt
    Added a text file tracking the issues for rework of the PCB (to Rev 1).
2020-04-14 Update PCB_Issues_For_Rework.txt
    Updated with LD1117-3.3 voltage regulator and clarification about not needing R7 and R8.
2020-05-11 Updated PCB Files
    Updated PCB files to Rev 1. Also updated data sheets and misc information, but the parts list is NOT updated in this commit.
    [RFID_Lock_PCB.brd, RFID_Lock_Rev_1_PCB.brd, RFID_Lock_Rev_1_PCB.sch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]
2020-05-13 Moved files to new repo
    Moved files to new Wireless_IO_Board repo. This repo will be dedicated to the use of the Wireless I/O board for controlling various cabinet locks.
    [RFID_Lock_Rev_1_PCB.brd, RFID_Lock_Rev_1_PCB.sch, Wireless_IO_Board_Parts_List.xlsx]
2020-06-04 Added photos and reorganized
    Just raw material here - needs cleanup and some explanation.
2020-07-10 Update RFID_Lock_Build_Instructions.pdf
    Added photos for mounting the pcb and the finished assembly.
2020-08-09 solenoid firmware v0.1
2020-08-28 Updates for Solenoid Lock
    Updated READme.md and Project Overview document to include the front door solenoid. Still need to work on build instructions and other HW documentation.
2020-08-30 Added build instructions for solenoid lock
    Added these instructions and updated the overview document to include this build instruction doc in its repo description.
2020-08-31 Update Solenoid_Lock_Build_Instructions.pdf
    Updated document with better photo of finshed project.
2021-04-26 v0.4 #define to prevent debugX events (untested)
    [mnutils.h, solenoidBox.ino]
2021-08-30 added antenna auto select
2021-09-07 solenoid hold time set to 4 seconds
